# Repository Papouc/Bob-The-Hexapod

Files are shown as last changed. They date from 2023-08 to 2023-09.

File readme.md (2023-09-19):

# Bob The Hexapod

Bob The Hexapod is an open source project that aims to present the hexapod platform using cheap and available parts. 

## Hardware

Entire robot is build using 3D printed parts and common electronic components.

Leg motion is handled by 18 SG90 servo motors driven by Raspberry Pi Pico board. The system is powered by DIY 2S li-ion battery pack. Most of the components are centralized on custom PCB board.

STEP files can be found under the [docs/3D](./docs/3D) folder. Similarly PCB gerber files are located in [docs/Gerber](./docs/Gerber).

All 3D parts were designed using Fusion 360 and are suitable for FDM printers. I've used PLA+ filament for mine but anything non-flexible will work. There are total of 58 printed parts needed for this build :D. 
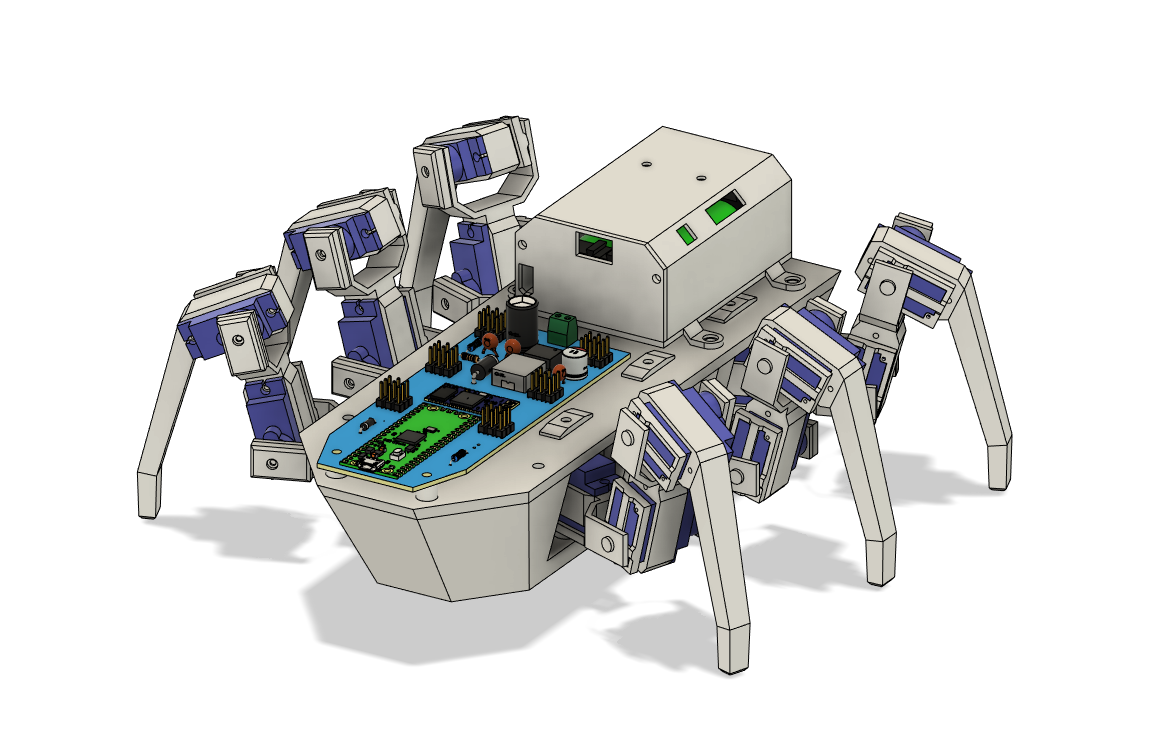
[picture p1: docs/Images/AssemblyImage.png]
Assembly


Battery pack is made out of 2 Sony US18650VTC5 li-ion cells in series protected by general 2S BMS circuit. Power output is handled by a pair of XT30 connectors.

Power supply is build around XL4015 IC. Circuit design is based on typical application circuit from its [datasheet](https://datasheet.lcsc.com/szlcsc/1811081616_XLSEMI-XL4015E1_C51661.pdf). Schematic is available in [docs/Gerber](./docs/Gerber) alongside gerber files.

### Basic parts list

As for electronics you will need the following:

- **Patience :D**
- Raspberry Pi Pico
- HC-05 bluetooth module
- 18 SG90 servos
- XL4015 buck converter IC
- 2 US18650VTC5 cells (or similar)
- Various resistor, capacitors and diodes

Detailed components BOM (bill of materials) is located in the [docs/Parts](./docs/Parts).

### Printed circuit board

PCB with 2 layers and thickness of 1.6mm is recommended. Soldermask color is not important for this board. Notice that trace width was increased due to higher current requirements. Stencil is not needed although it is better to use one for handful of present SMD parts.

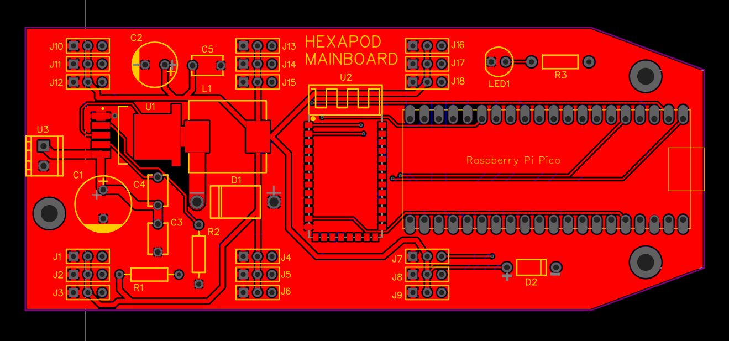
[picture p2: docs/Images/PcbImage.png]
PCB


## Software

RPI board was programmed using [PlatformIO](https://platformio.org) and [Arduino-Pico core](https://arduino-pico.readthedocs.io/en/latest). Source code is located in this repository in [src](./src) folder with dependencies in [lib](./lib). Whole project is written in object oriented C++.

There is custom wrapper library for servo control included. Purpose of this addition is to get seamless control over 18 servos by combining PWM channels of RPI pico with PIO based servo control *(RP2040 has max of 16 independent PWM channels)*.

Leg movement is controled by simple inverse kinematics written only for femur and tibia joints (coxa joint si controlled by setting specific angle). This logic is present in [Leg.cpp](./src/Leg.cpp) file.

At the moment, the robot is supposed to be controlled by an Android phone via bluetooth. This [app](https://play.google.com/store/apps/details?id=braulio.calle.bluetoothRCcontroller&pcampaignid=web_share) was used for testing.

## Result

This photo shows fully assembled and programmed *Bob The Hexapod* in action. 

Currently it has a problem with walking on slippery surfaces, but it should be easily resolved by adding rubber feet attachments.

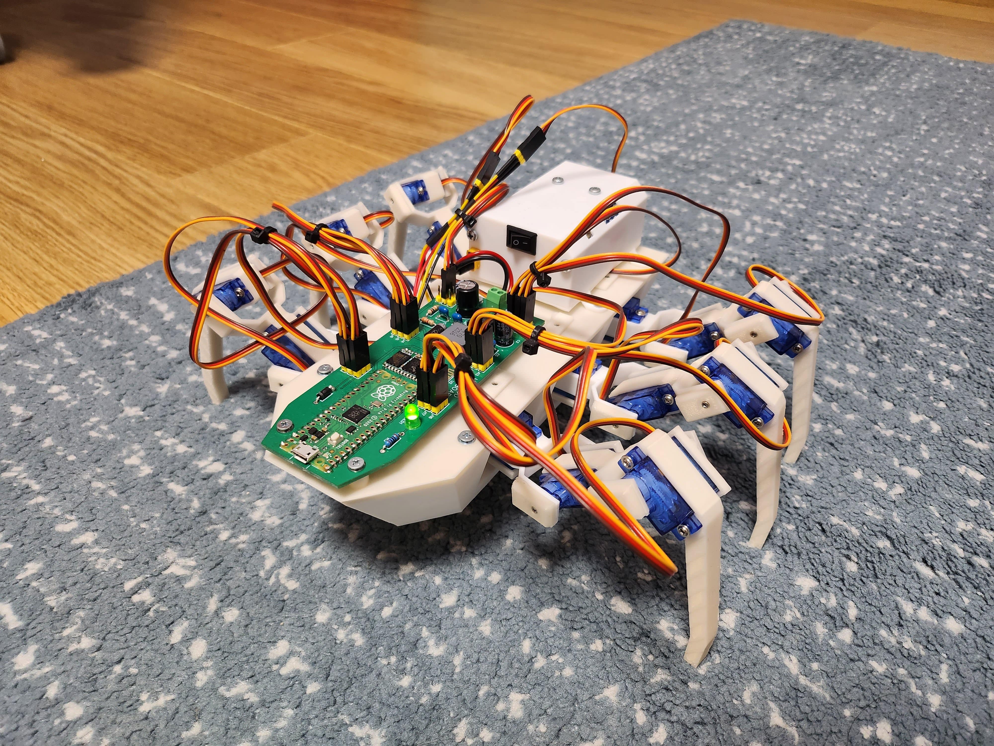
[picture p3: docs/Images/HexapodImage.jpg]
Hexapod


I hope you like the project :D!!

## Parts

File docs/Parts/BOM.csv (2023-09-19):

ID | Name | Designator | Footprint | Quantity
1 | RASPBERRY-PI-PICO | 1 | RASPBERRYPIPICO | 1
2 | 220uF | C1 | CAP-TH_BD10.0-P5.00-D1.0-FD | 1
3 | 330uF | C2 | CAP-TH_BD8.0-P3.50-D0.6-FD | 1
4 | 1uF | C3,C4,C5 | CAP-TH_L5.5-W3.5-P5.00-D1.2 | 3
5 | SB540_C268686 | D1 | DO-201AD_BD5.3-L8.4-P12.50-D1.4-RD | 1
6 | 1N5819_C84620 | D2 | DO-41_BD2.4-L4.7-P8.70-D0.9-RD | 1
7 | SERVO_0 | J1 | HDR-M-2.54_1X3 | 1
8 | SERVO_1 | J2 | HDR-M-2.54_1X3 | 1
9 | SERVO_2 | J3 | HDR-M-2.54_1X3 | 1
10 | SERVO_3 | J4 | HDR-M-2.54_1X3 | 1
11 | SERVO_4 | J5 | HDR-M-2.54_1X3 | 1
12 | SERVO_5 | J6 | HDR-M-2.54_1X3 | 1
13 | SERVO_6 | J7 | HDR-M-2.54_1X3 | 1
14 | SERVO_7 | J8 | HDR-M-2.54_1X3 | 1
15 | SERVO_8 | J9 | HDR-M-2.54_1X3 | 1
16 | SERVO_9 | J10 | HDR-M-2.54_1X3 | 1
17 | SERVO_10 | J11 | HDR-M-2.54_1X3 | 1
18 | SERVO_11 | J12 | HDR-M-2.54_1X3 | 1
19 | SERVO_12 | J13 | HDR-M-2.54_1X3 | 1
20 | SERVO_13 | J14 | HDR-M-2.54_1X3 | 1
21 | SERVO_14 | J15 | HDR-M-2.54_1X3 | 1
22 | SERVO_15 | J16 | HDR-M-2.54_1X3 | 1
23 | SERVO_16 | J17 | HDR-M-2.54_1X3 | 1
24 | SERVO_17 | J18 | HDR-M-2.54_1X3 | 1
25 | 47uH | L1 | IND-SMD_L13.5-W12.5 | 1
26 | LED-TH-5mm_G | LED1 | LED-TH_BD5.0_GREEN | 1
27 | 10kΩ | R1 | RES-TH_BD2.3-L6.5-P10.50-D0.5 | 1
28 | 3.3kΩ | R2 | RES-TH_BD2.2-L6.5-P10.50-D0.6 | 1
29 | 330Ω | R3 | R_AXIAL-0.4 | 1
30 | XL4015E1 | U1 | TO-263-5_L10.2-W8.9-P1.70-TL | 1
31 | HC-05 | U2 | BT34P-SMD-1.5-26.9X13.0X2.2MM | 1
32 | DG350-3.5-02P-14-00A(H) | U3 | CONN-TH_DG350-3.5-02P-14-00A-H | 1

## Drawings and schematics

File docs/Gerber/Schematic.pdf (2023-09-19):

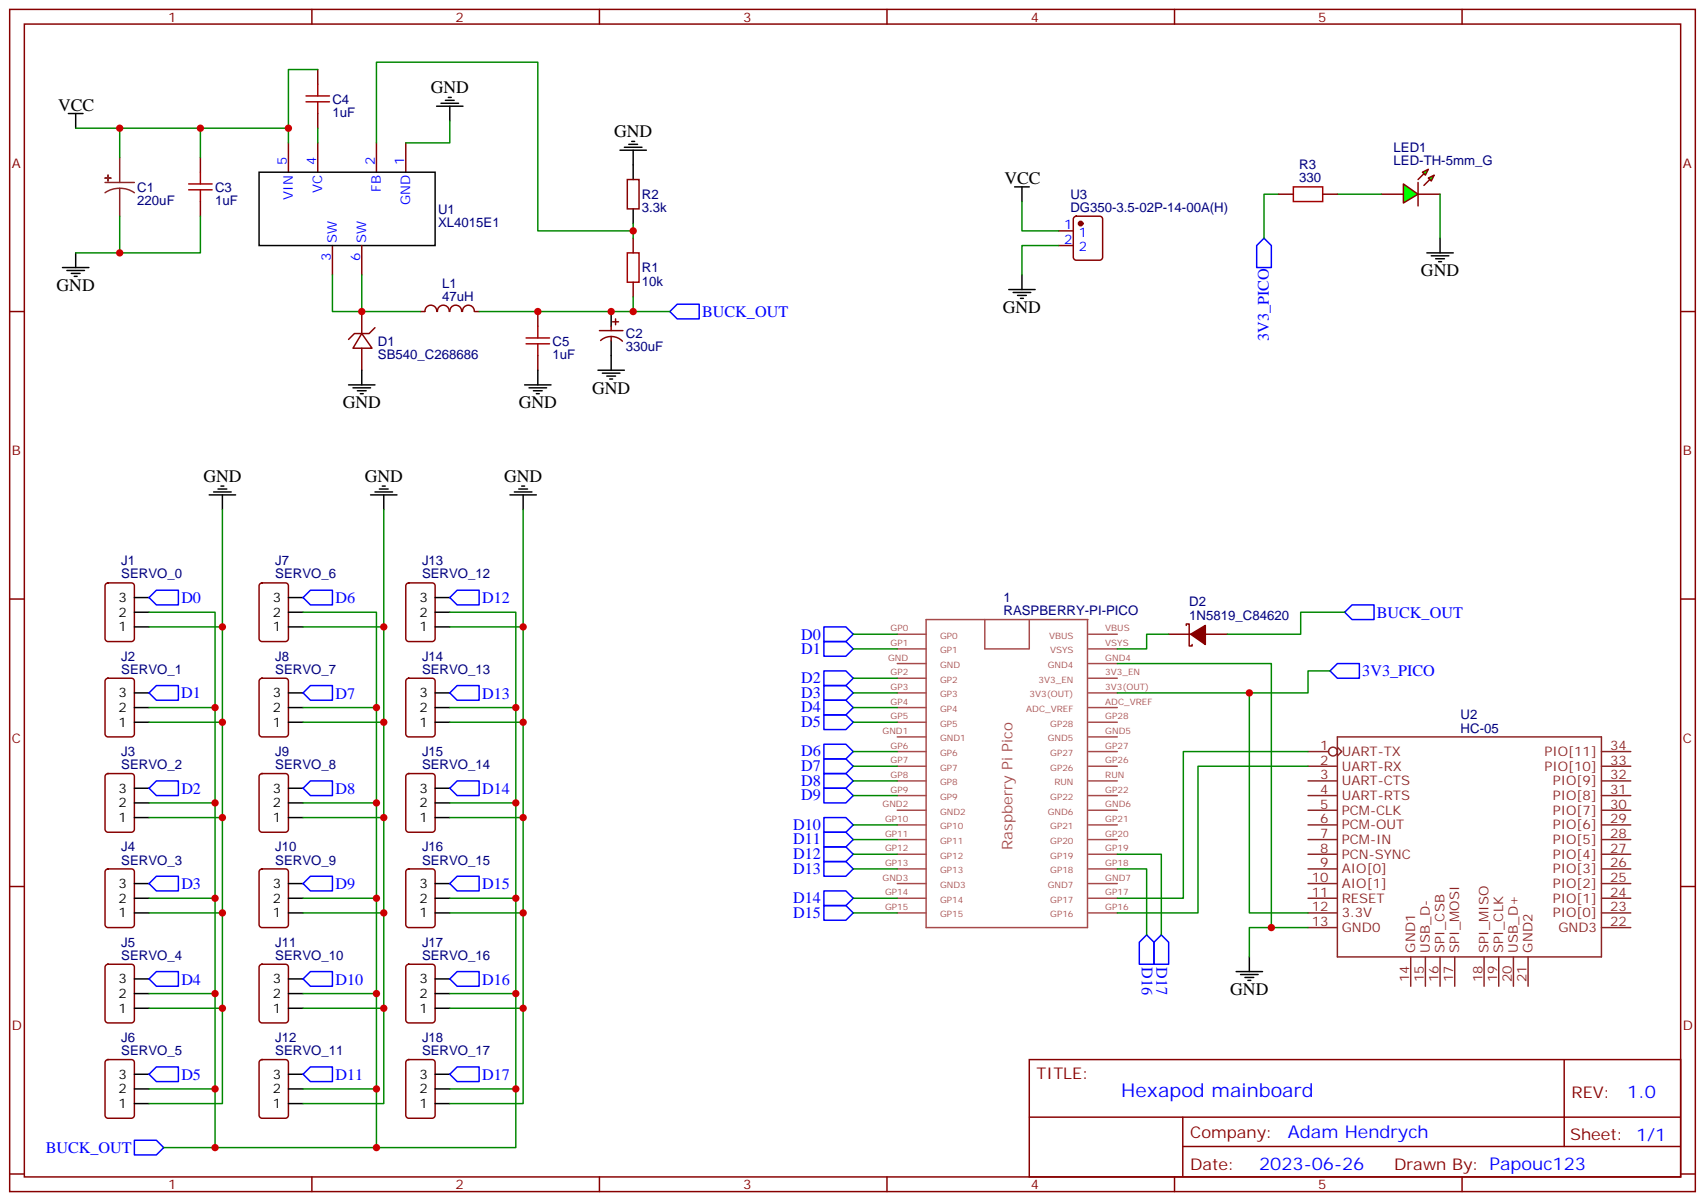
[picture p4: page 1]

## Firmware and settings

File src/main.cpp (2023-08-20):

#include <Arduino.h>
#include "Body.h"
#include "BtReciever.h"
#include "PinLayout.h"

#define TIMER_PERIOD 5

Body *_Body = nullptr;
BtReciever *_Reciever = nullptr;

ulong prevMillis;
ulong currMillis;

void setup()
{
    _Body = new Body();
    _Body->ReachInitialPosition();

    _Reciever = new BtReciever(SERIAL_RX_PIN, SERIAL_TX_PIN);

    delay(1000);

    prevMillis = millis();
}

void loop()
{
    currMillis = millis();

    char data = _Reciever->GetData();

    if (_Body->IsOnPosition())
    {
        // ready for next move
        switch (data)
        {
        case 'F':
            _Body->SetNextStepPosition(Direction::FORWARD);
            break;
        case 'B':
            _Body->SetNextStepPosition(Direction::BACKWARD);
            break;
        case 'L':
            _Body->SetNextTurnPosition(Rotation::LEFT);
            break;
        case 'R':
            _Body->SetNextTurnPosition(Rotation::RIGHT);
            break;
        case FIRST_CONNECT:
            _Body->SetStancePosition();
            break;
        case DISCONNECT:
            _Body->ReachInitialPosition();
            break;
        }
    }

    if (currMillis - prevMillis >= TIMER_PERIOD)
    {
        _Body->MoveToPosistion();
        prevMillis = currMillis;
    }
}

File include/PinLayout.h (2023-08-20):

#pragma once

#define LEG_1_COXA_PIN 11
#define LEG_1_FEMUR_PIN 10
#define LEG_1_TIBIA_PIN 9

#define LEG_2_COXA_PIN 14
#define LEG_2_FEMUR_PIN 13
#define LEG_2_TIBIA_PIN 12

#define LEG_3_COXA_PIN 19
#define LEG_3_FEMUR_PIN 18
#define LEG_3_TIBIA_PIN 15

#define LEG_4_COXA_PIN 0
#define LEG_4_FEMUR_PIN 1
#define LEG_4_TIBIA_PIN 2

#define LEG_5_COXA_PIN 3
#define LEG_5_FEMUR_PIN 4
#define LEG_5_TIBIA_PIN 5

#define LEG_6_COXA_PIN 6
#define LEG_6_FEMUR_PIN 7
#define LEG_6_TIBIA_PIN 8

#define SERIAL_RX_PIN 17
#define SERIAL_TX_PIN 16

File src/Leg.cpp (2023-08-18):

#include "Leg.h"

Leg::Leg(byte coxaPin, byte femurPin, byte tibiaPin, bool left)
{
    _CoxaJoint = new ServoMotor(coxaPin);
    _FemurJoint = new ServoMotor(femurPin);
    _TibiaJoint = new ServoMotor(tibiaPin);

    _Left = left;
}

Leg::~Leg()
{
    delete _CoxaJoint;
    delete _FemurJoint;
    delete _TibiaJoint;
}

void Leg::SetDefaultPos(int coxaAngle, int femurAngle, int tibiaAngle)
{
    _CoxaInfo.JointBase = coxaAngle;
    _CoxaInfo.JointPrevious = coxaAngle;
    _CoxaInfo.JointCurrent = coxaAngle;

    _FemurInfo.JointBase = femurAngle;
    _FemurInfo.JointPrevious = femurAngle;
    _FemurInfo.JointCurrent = femurAngle;

    _TibiaInfo.JointBase = tibiaAngle;
    _TibiaInfo.JointPrevious = tibiaAngle;
    _TibiaInfo.JointCurrent = tibiaAngle;

    (*_CoxaJoint).write(coxaAngle);
    (*_FemurJoint).write(femurAngle);
    (*_TibiaJoint).write(tibiaAngle);
}

void Leg::DetermineServoAngles(Point point)
{
    DetermineServoAngles(point, _CoxaInfo.JointCurrent);
}

void Leg::DetermineServoAngles(Point point, int coxaAngle)
{
    // direction values

    double input = sqrt(pow(point.X, 2) + pow(point.Z, 2));
    double baseAngle = degrees(atan(point.X / point.Z));

    // femur angle value

    double femurAngle = degrees(
        acos(
            (pow(TIBIA_FOOT_DISTANCE, 2) - pow(FEMUR_TIBIA_DISTANCE, 2) - pow(input, 2)) /
            (-2 * FEMUR_TIBIA_DISTANCE * input)));

    // tibia angle value

    double tibiaAngle = degrees(
        asin((input * sin(radians(femurAngle))) / TIBIA_FOOT_DISTANCE) +
        asin((LEG_BEND_DISTANCE * sin(radians(LEG_BEND_ANGLE))) / TIBIA_FOOT_DISTANCE));

    // final values for servos

    short sideConstant = _Left ? 1 : -1;

    int coxaToWrite = _CoxaInfo.JointBase + (sideConstant * coxaAngle);

    int femurToWrite = _FemurInfo.JointBase + sideConstant * (180 - (baseAngle + femurAngle));

    int tibiaToWrite = _TibiaInfo.JointBase + sideConstant * (90 - tibiaAngle);

    // save destination values

    _CoxaInfo.JointDestination = coxaToWrite;
    _FemurInfo.JointDestination = femurToWrite;
    _TibiaInfo.JointDestination = tibiaToWrite;

    OnPosition = false;
}

void Leg::ExecuteMovement()
{
    _CoxaInfo.JointCurrent = (_CoxaInfo.JointDestination * 0.05) + (_CoxaInfo.JointPrevious * 0.95);
    _CoxaInfo.JointPrevious = _CoxaInfo.JointCurrent;

    _FemurInfo.JointCurrent = (_FemurInfo.JointDestination * 0.05) + (_FemurInfo.JointPrevious * 0.95);
    _FemurInfo.JointPrevious = _FemurInfo.JointCurrent;

    _TibiaInfo.JointCurrent = (_TibiaInfo.JointDestination * 0.05) + (_TibiaInfo.JointPrevious * 0.95);
    _TibiaInfo.JointPrevious = _TibiaInfo.JointCurrent;

    (*_CoxaJoint).write(_CoxaInfo.JointCurrent);
    (*_FemurJoint).write(_FemurInfo.JointCurrent);
    (*_TibiaJoint).write(_TibiaInfo.JointCurrent);

    OnPosition = abs(_CoxaInfo.JointDestination - _CoxaInfo.JointCurrent) < 0.2 &&
                 abs(_FemurInfo.JointDestination - _FemurInfo.JointCurrent) < 0.2 &&
                 abs(_TibiaInfo.JointDestination - _TibiaInfo.JointCurrent) < 0.2;
}

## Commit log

2023-07-31 Initial commit :tada:
    - PlatformIO project setted up
    - Added my rpi pico library for controling up to 24 servos
2023-08-04 Inverse kinematics
    - implemented inverse kinematics model for leg geometry
    - added stance position
    - added servo movement smoothing
2023-08-18 Added direction control :sparkles:
    - support for walking backwards
    - added direction enum
    - minor typing error fix
    [Body.cpp, Leg.cpp, main.cpp]
2023-08-20 Bluetooth control :boom:
    - Full movement control via bluetooth
    - BT communication over RPI pico hardware UART0
    - Stands up on successful connection
2023-09-19 Added readme and project resources :bento:
    - added project description
    - new 3D step files
    - images for readme
    - gerber files for PCB
    - BOM list for necessary parts
    [BOM.csv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]
